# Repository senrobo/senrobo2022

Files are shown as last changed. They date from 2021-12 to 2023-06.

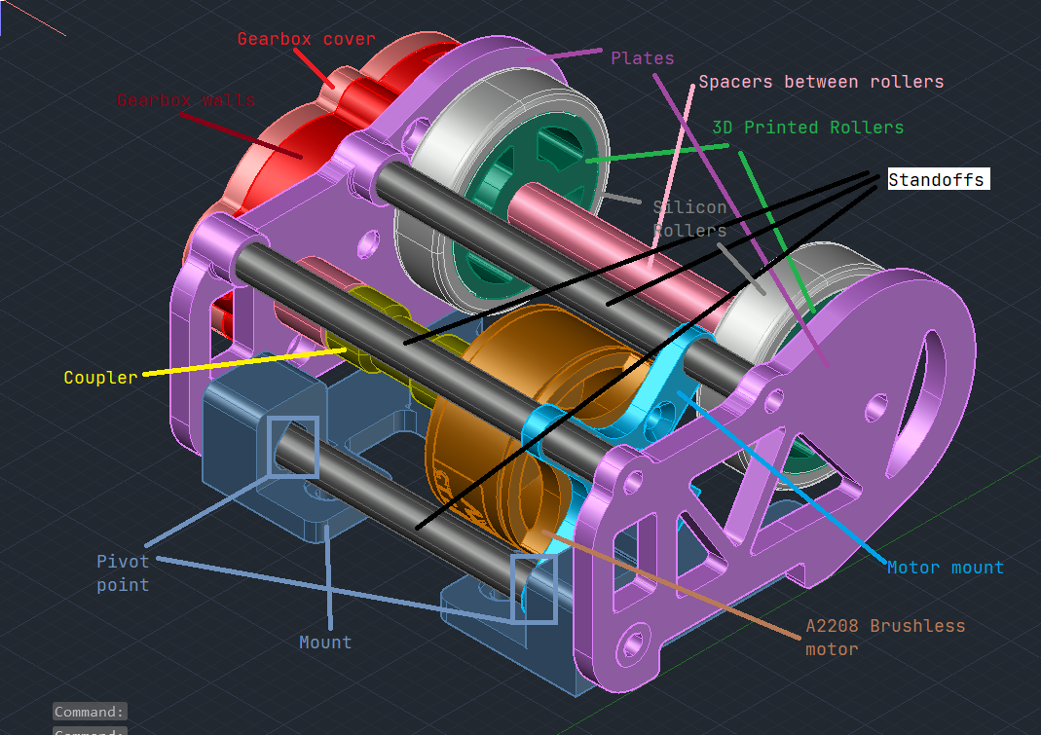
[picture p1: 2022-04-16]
logbook/dribbler5.png

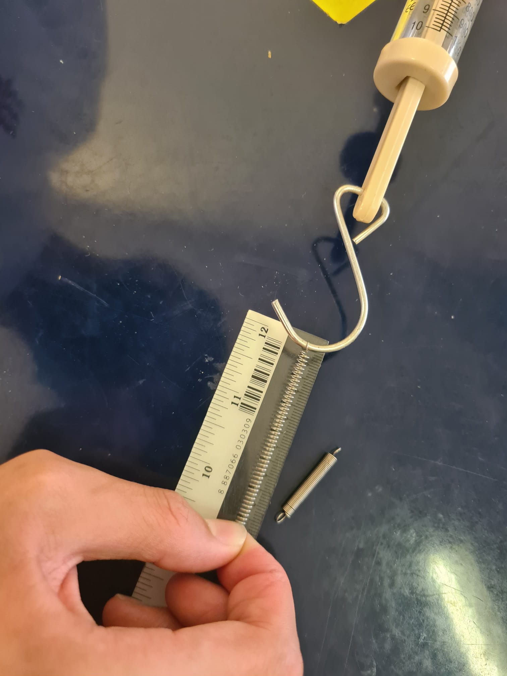
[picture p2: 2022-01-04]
research/spring-test.jpeg

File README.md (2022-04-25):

# Sentinels Robotics

Yay we passed the 100th commit milestone
400 Commit milestone

## Checklist

### Mechanical

- Kicker Done on 20/1/2022

### Parts used

| Part Name | Part Description |
| --- | --- |
| OpenMV H7/R7 | Camera |
| MUX | Multiplexer (https://www.ti.com/lit/ds/symlink/cd74hc4067.pdf) |

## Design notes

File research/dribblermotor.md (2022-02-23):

 10 :40pm: Dribbler motor was too fat and heavy, although it met criteria, it does not meet the weight

had to find for alternatives

went online and read up

basically this website has the impt shit

https://www.rotordronepro.com/understanding-kv-ratings/

so, the higher the KV = more heat = sucks ass = weak ass torque cos the whatever RPM stupid shit is like fucking calculated when the motor is "free moving" so the motor is not underload which is not what we want as our dribbler is always under load

asked the seniors why they were using a super low kv motor 820kV

referred to other lw teams and saw that they were using the A2208 not the A2212 which i was considering to use

shit is fucking autism

why the senior gear down cos the Open ball light as fuck

11:52pm : Now senior said the dribbler is useless cos the matches are all so fast fucking pased what fuck

why am i here just to suffer

<hr></hr>

###### Bern Jia Min Luo Yee Haw *—* 26/11/2021 at 11:56 PM

and vibrations become amplified at such high speeds

###### jh *—*  26/11/2021at 11:56 PM

   anw ir ball need higher rpm

   smaller motor usually rpm bigger so

   maybe ur gearing wont even have to change at all

   win

<hr></hr>

in conclusion, 

###### beanstalk *—* 26/11/2021 at 11:56 PM

lightweight matches are super fast paced lol if they ram into u and your dribbler is shit and loses control of the ball then there really isnt a point in having 1

Vincent - 11/26/2021

what tf its aldy 12

taobao time ezpz

its not ezpz

stupid piece of shit

Vincent11/27/2021

Fuck dribbler not enough space

Vincent 4/1/2022

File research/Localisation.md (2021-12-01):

# Why we dont fucking use ultrasonic

The teensy doesnt output 5V but the ultrasonic sensor need 3.3V volt

Considered usinng logic level converter but quite stupid

So condluded to use camera + compass localisation

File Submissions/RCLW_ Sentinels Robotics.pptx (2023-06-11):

## Sentinels

Hwa Chong Institution

Vincent Cayadi, Zhu Yunsong

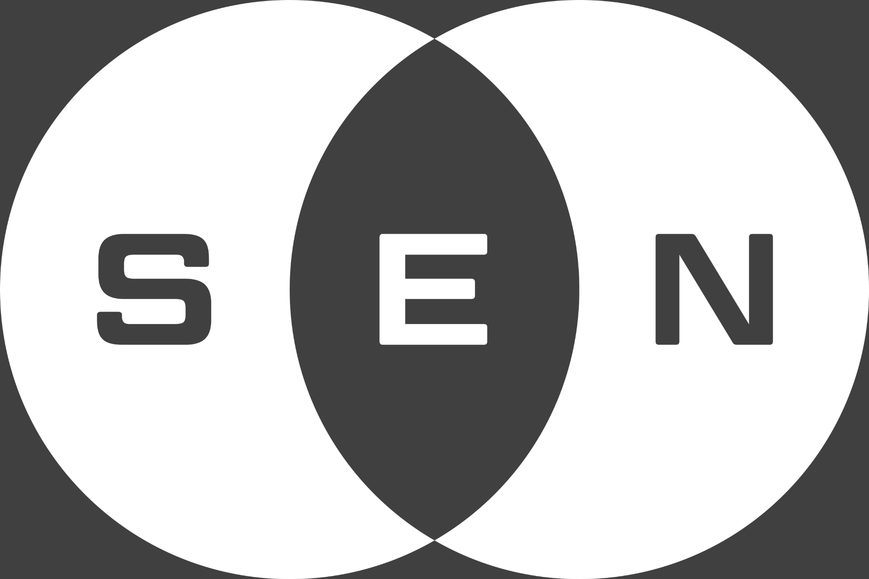
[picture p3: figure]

## Table of contents 1/ Introduction 2/ Mechanical 3/ Electrical 4/ Programming

Background information about our team

Hardware and design aspect of our robot

PCB Design and electronics

Program and algorithms of out robot

## Intro- duction 1/

The 2 man team from Hwa Chong Institution

## Mechanical 2/

Mechanism and elements of our robot

## Layer 1

- Motor
- Slope

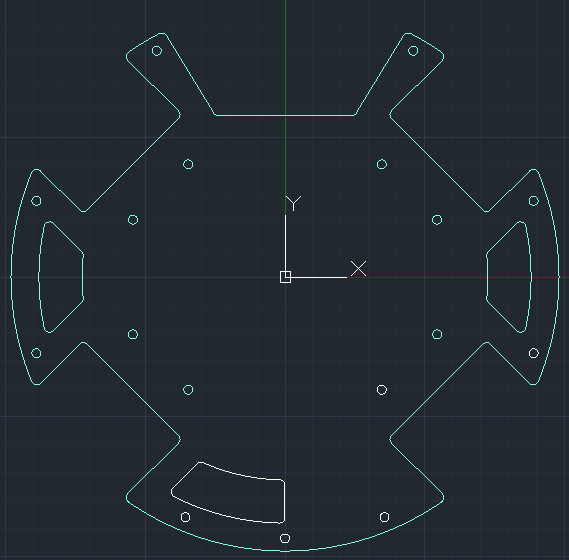
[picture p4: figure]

## Motor Layout Omni-directional 45° Layout

Wheels are 3D printed, with rubber rollers perpendicular to the wheel to make it omnidirectional

Such a layout allows the robot to move in all directions by controlling speed, power and direction of each individual wheel.

## Layer 2

- Dribbler with catchment area in front
- Rec. hole on left for jumper cable
- Rec. hole in center for kicker rack
- Rec. hole on right for servo
- Hole at the back for battery mount

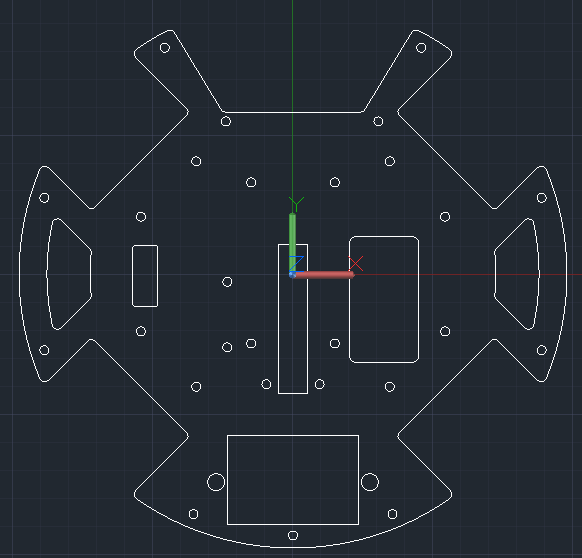
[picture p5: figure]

## Layer 3

Houses our brains
Teensy 4.0 located here
IR Sensor placed here for the highest point of the ball
Camera is also located here
Have a 5 point connection to layer 2 so that the camera won't be shakey

- Copy this slide

## Problems

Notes: Taobao and Senior hogging the printers

## Electrical 3/

Elec go boom

## Schematic

- Layer 1
- Unchanged
- Layer 2
- GND Plane
- Layer 3
- Compass elec shoved there
- Layer 4
- Removed all the elec

## PCB : Layer 1

- LED Ring
- Motor Drivers
- 5V Step Down
- 3V Step Down

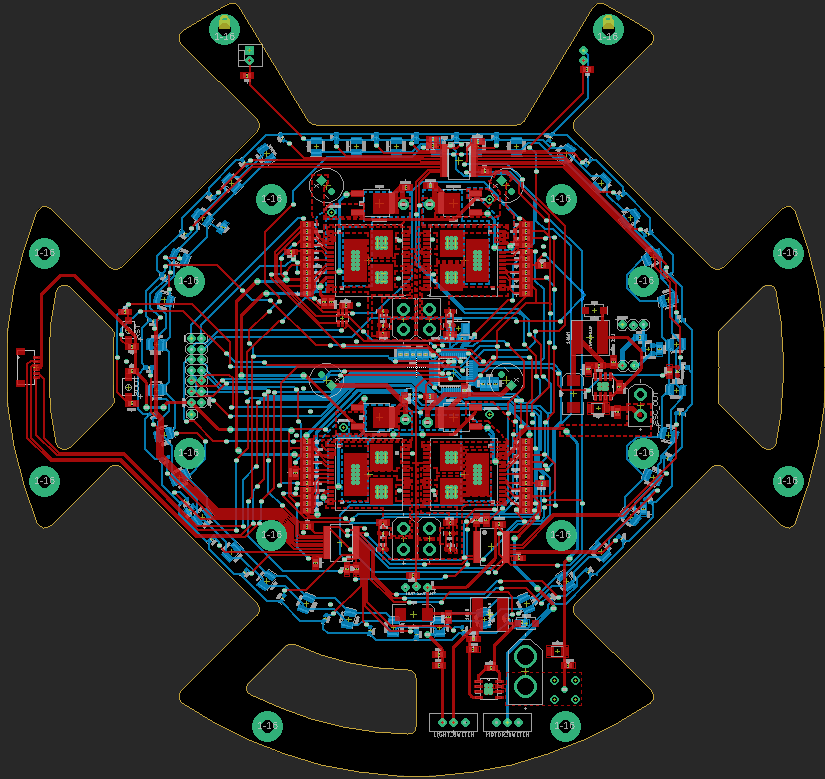
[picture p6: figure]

## PCB : Layer 2

- GND Plane
  - Block Off the Electromagnetic field of the Motor to shield the compass from the field

## PCB : Layer 3

- IR Sensors
- OpenMV Camera
- Compass Components

## Programming: Conceptual 4/

## Camera Localisation

- Removed TOF so how?
- <insert transcendence pic>

## Closing Thoughts

## Thanks!

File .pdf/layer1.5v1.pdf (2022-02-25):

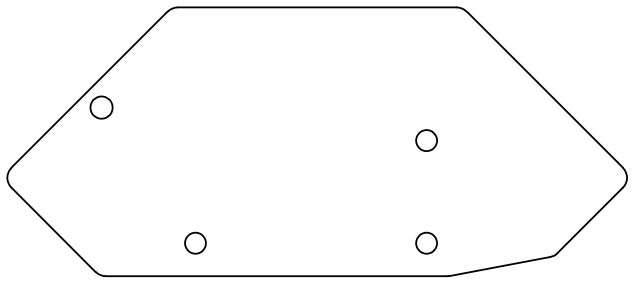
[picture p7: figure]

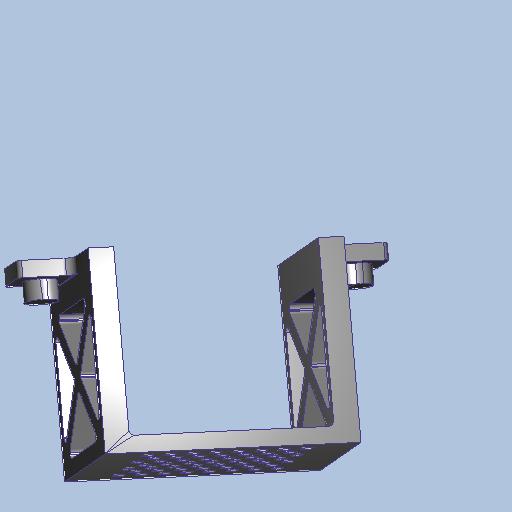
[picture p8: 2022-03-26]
.stl/test/Design 1/Scenario 1/thumbnail.jpg

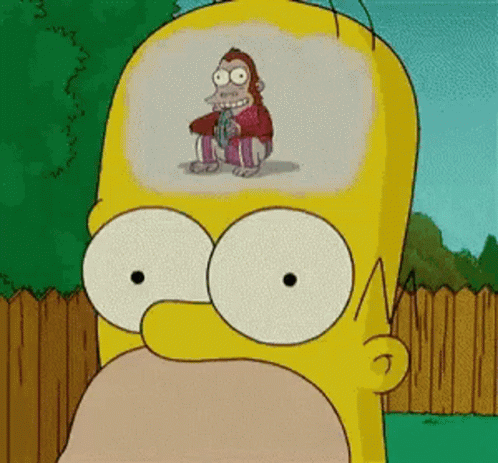
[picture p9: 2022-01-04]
research/homermonkey.gif

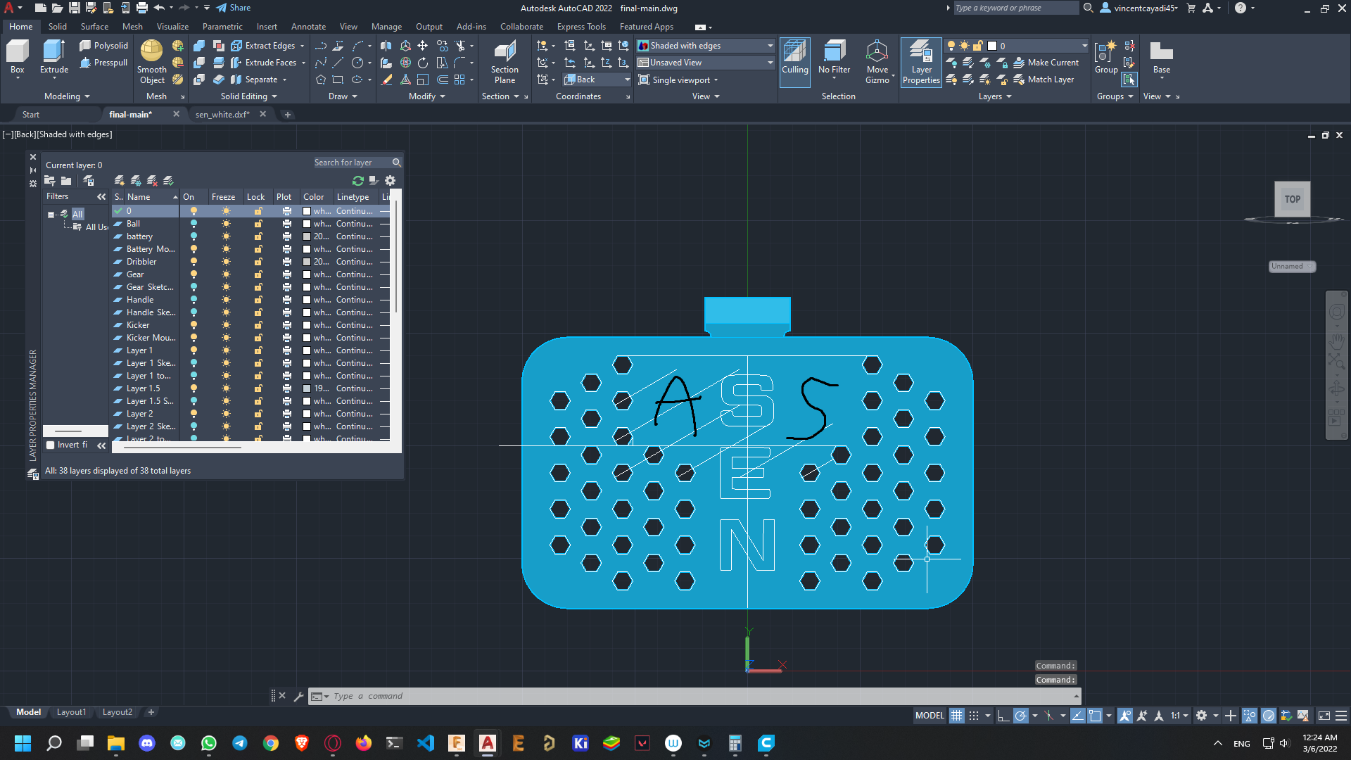
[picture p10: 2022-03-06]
research/senAss.png

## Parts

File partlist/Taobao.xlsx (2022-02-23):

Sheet: Mech
Part Type | Part Name | Decription | Source | Unit Price (¥) | Quantity needed | Quantitiy bought | Total Price (¥) | Total Price (SGD)
Aluminium Stands | M3*37 D=5mm | Stands from Layer 1 to 2 | https://item.taobao.com/item.htm?spm=a1z09.2.0.0.1df82e8d7MtmSg&id=544763051390&_u=230vu5iq6340 | ¥1.50 | 8 | 0 | ¥12.00 | $2.40
Aluminium Stands |  | Stands from Layer 2 to 3 | https://item.taobao.com/item.htm?spm=a1z09.2.0.0.1df82e8d7MtmSg&id=544763051390&_u=230vu5iq6340 | ¥0.00 | 0 | 0 | ¥0.00 | $0.00
Aluminium Stands | M3*20 D=5mm | Front Kicker | https://item.taobao.com/item.htm?spm=a1z09.2.0.0.1df82e8d7MtmSg&id=544763051390&_u=230vu5iq6340 | ¥1.20 | 2 | 0 | ¥2.40 | $0.48
Aluminium Stands | M3*15 D=5mm | Back Kicker | https://item.taobao.com/item.htm?spm=a1z09.2.0.0.1df82e8d7MtmSg&id=544763051390&_u=230vu5iq6340 | ¥1.00 | 2 | 0 | ¥2.00 | $0.40
Metal Nuts |  | a lot |  | ¥0.00 | 0 | 0 | ¥0.00 | $0.00
M3 Screws |  | a lot |  | ¥0.00 | 0 | 0 | ¥0.00 | $0.00
Headless screws |  | a lot |  | ¥0.00 | 0 | 0 | ¥0.00 | $0.00
Extension Springs | 0.4*4*30 | Kicker Mechanism | https://item.taobao.com/item.htm?spm=a1z09.2.0.0.61472e8dM5d2jk&id=522768077711&_u=n30vu5iqd1c4&mt= | ¥3.25 | 1 | 0 | ¥3.25 | $0.65
Servo | MG90S | Servo For kicker |  | ¥0.00 | 0 | 0 | ¥0.00 | $0.00
Heat Sinks | 散热片 8.8*8.8*5MM (黑色) | Heatsink for Motor Driver | https://item.taobao.com/item.htm?id=565186396799&ns=1&abbucket=14 (https://item.taobao.com/item.htm?spm=a230r.1.14.21.5b804308qjOPfB&id=565186396799&ns=1&abbucket=14) | ¥0.24 | 16 | 0 | ¥3.84 | $0.77

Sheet: Elec - Layer 1
Qty | Value | Device | Package | Parts | Description | PROD_ID | SF_ID | SF_SKU | VALUE.1 | Column1
2 | 220uF | 100UF-POLAR-EIA7343-10V-10%(TANT) | EIA7343 | 1C4, 1C7 | 100ÂµF polarized capacitors | CAP-07890 |  |  | 100uF
12 | 18AWG | 18AWG | 18AWG | GND_M2A, GND_M2B, GND_M4A, GND_M4B, V_BATT_M1A, V_BATT_M1B, V_BATT_M2A, V_BATT_M2B, V_BATT_M3A, V_BATT_M3B, V_BATT_M4A, V_BATT_M4B
4 | 680uF | 3.5MM_CAP | 3.5MM_CAP | M1C2, M2C2, M3C2, M4C2
36 | 3528LED | 3528LED | 3528 | LD1, LD2, LD3, LD4, LD5, LD6, LD7, LD8, LD9, LD10, LD11, LD12, LD13, LD14, LD15, LD16, LD17, LD18, LD19, LD20, LD21, LD22, LD23, LD24, LD25, LD26, LD27, LD28, LD29, LD30, LD31, LD32, LD33, LD34, LD35, LD36
3 |  | 74HC4067SSOP-24 | SSOP24 | MUX_L1, MUX_L2, MUX_L3
7 | 0.1uF | CAPACITOR0603 | C0603 | 1C5, 1C9, 2C1, 2C2, 2C3, 3C1, 3C2
4 | 1.0uF | CAPACITOR0603 | C0603 | M1C3, M2C3, M3C3, M4C3
3 | 10nF | CAPACITOR0603 | C0603 | 1C3, 1C8, C4
14 | 1uF | CAPACITOR0603 | C0603 | 2C4, 2C5, 2C6, C1, C2, C3, C5, C8, LC1, LC2, LC3, LC4, LC5, LC6
2 | 22pF | CAPACITOR0603 | C0603 | C6, C7
4 | 33nF | CAPACITOR0603 | C0603 | M1C1, M2C1, M3C1, M4C1
2 | 4.7uF | CAPACITOR0603 | C0603 | 1C1, 1C6
2 | 22uF | CAPACITOR1210 | C1210 | 1C2, 1C10
1 |  | CONN_021X02_NO_SILK | 1X02_NO_SILK | LDR | Multi connection point. Often used as Generic Header-pin footprint for 0.1 inch spaced/style header connections
1 |  | CONN_02LOCK | 1X02_LOCK | J1 | Multi connection point. Often used as Generic Header-pin footprint for 0.1 inch spaced/style header connections
1 |  | CONN_02POLAR | MOLEX-1X2 | LED | Multi connection point. Often used as Generic Header-pin footprint for 0.1 inch spaced/style header connections |  | PRT-09918
1 |  | CONN_03LOCK | 1X03_LOCK | ESC_IN | Multi connection point. Often used as Generic Header-pin footprint for 0.1 inch spaced/style header connections
1 | CONN_07X2 | CONN_07X2 | 2X7 | U$15
1 | 8MHz | CRYSTALSMD-5X3.2-2PAD | CRYSTAL-SMD-5X3.2-2PAD | Y1 | Crystals (Generic)
2 | SS54 | DIODE-SCHOTTKY | SMA-DIODE | 1D1, 1D2
2 | 30Î©/1.8A | FERRITE_BEAD-0603 | 0603 | FB1, FB2 | Ferrite Bead (blocks, cores, rings, chokes, etc.) | NDUC-13805 |  |  | 30Î©/1.8A
2 | 10uH | INDUCTORSWPA8040 | SWPA8040 | 1L1, 1L2
1 | STM_LED | LED0603 | LED-0603 | D1 | LED (Generic)
4 | BLUE | LED-BLUE0603 | LED-0603 | M1D2, M2D2, M3D2, M4D2 | Blue SMD LED | DIO-08575 |  |  | BLUE
4 | RED | LED-RED0603 | LED-0603 | M1D1, M2D1, M3D1, M4D1 | Red SMD LED | DIO-00819 |  |  | RED
36 |  | LIGHT_SENSORALS | ALS-PT19 | Q1, Q2, Q3, Q4, Q5, Q6, Q7, Q8, Q9, Q10, Q11, Q12, Q13, Q14, Q15, Q16, Q17, Q18, Q19, Q20, Q21, Q22, Q23, Q24, Q25, Q26, Q27, Q28, Q29, Q30, Q31, Q32, Q33, Q34, Q35, Q36 | Ambient Light Sensors - Phototransistors | IC-11836 | SEN-12566
2 | MOMENTARY_SWITCH_4X3 | MOMENTARY_SWITCH_4X3 | MOMENTARY_SWITCH_4X3 | BOOT, RST
1 | AO3402 | MOSFET-NCH-AO3404A | SOT23-3 | Q37 | N-channel MOSFETs | TRANS-12988 |  |  | 5.8A/30V/35mÎ©
4 | AOD482 | MOSFET-NCH-FDD8780 | DPAK | M1Q1, M2Q1, M3Q1, M4Q1 | N-channel MOSFETs | TRANS-09984 |  |  | 35A/25V/8.5mÎ©
16 | 10k | RESISTOR0603 | R0603 | 1R1, 1R3, M1R8, M1R9, M1R11, M2R8, M2R9, M2R11, M3R8, M3R9, M3R11, M4R8, M4R9, M4R11, R1, R4
29 | 1k | RESISTOR0603 | R0603 | 2R1, 2R2, 2R3, M1R1, M1R2, M1R5, M1R6, M1R7, M1R10, M2R1, M2R2, M2R5, M2R6, M2R7, M2R10, M3R1, M3R2, M3R5, M3R6, M3R7, M3R10, M4R1, M4R2, M4R5, M4R6, M4R7, M4R10, R2, R3
1 | 2M | RESISTOR0603 | R0603 | R6
1 | 2k | RESISTOR0603 | R0603 | LG_R2
1 | 3.24k | RESISTOR0603 | R0603 | 1R4
8 | 3.3k | RESISTOR0603 | R0603 | M1R3, M1R4, M2R3, M2R4, M3R3, M3R4, M4R3, M4R4
3 | 3k | RESISTOR0603 | R0603 | 2R4, 2R5, 2R6
6 | 4.7k | RESISTOR0603 | R0603 | M1R12, M2R12, M3R12, M4R12, R8, R9
1 | 47 | RESISTOR0603 | R0603 | LR1
1 | 470 | RESISTOR0603 | R0603 | R5
1 | 5.9k | RESISTOR0603 | R0603 | 1R2
1 | 500k | RESISTOR0603 | R0603 | R7
1 | SM06B-SRSS-TB | SM06B-SRSS-TB | SM06B-SRSS-TB | X2 | JST SH series header 1.00mm pitch disconnectable crimp style connectors, horizontal (side entry type), 6 pins
2 |  | SN74LVC2G04DBVR | SOT23-6 | MU1, MU2
1 | STM32F103CBT6 | STM32F103CBT6 | LQFP48 | U$2
2 |  | SWITCH-SPDT-PTH-11.6X4.0MM-LOCK | SWITCH_SPDT_PTH_11.6X4.0MM_LOCK | LIGHT_SWITCH, MOTOR_SWITCH | Single Pole, Double Throw (SPDT) Switch | SWCH-08261 |  | COM-00102
2 |  | TPS54X0 | POWERPAD-SOIC-8 | U1, U2
4 | VNH5019 | VNH5019 | POWERSO-30 | M_BL, M_BR, M_FL, M_FR
5 | XT30PB-F | XT30PB-F | XT30PB-F | ESC_OUT, M1J1, M2J1, M3J1, M4J1
1 | XT60XT60PB-M | XT60XT60PB-M | XT60PB-M | U$1

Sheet: Elec - Layer 3
Qty | Value | Device | Package | Parts | Description | PROD_ID | SF_SKU | VALUE.1 | Column1
24 |  | CAPACITOR0603 | C0603 | 3C1, 3C2, 3C3, 3C4, 3C5, 3C6, 3C7, 3C8, 3C9, 3C10, 3C11, 3C12, 3C13, 3C14, 3C15, 3C16, 3C17, 3C18, 3C19, 3C20, 3C21, 3C22, 3C23, 3C24
4 | 1uF | CAPACITOR0603 | C0603 | C1, C2, C3, C5
2 | 22pF | CAPACITOR0603 | C0603 | C6, C7
1 |  | CONN_02LOCK | 1X02_LOCK | J1 | Multi connection point. Often used as Generic Header-pin footprint for 0.1 inch spaced/style header connections
1 |  | CONN_03LOCK | 1X03_LOCK | SERVO_IO | Multi connection point. Often used as Generic Header-pin footprint for 0.1 inch spaced/style header connections
1 | CONN_07X2 | CONN_07X2 | 2X7 | U$14
1 | 8MHz | CRYSTALSMD-5X3.2-2PAD | CRYSTAL-SMD-5X3.2-2PAD | Y1 | Crystals (Generic)
1 | DIP-04SMD | DIP-04SMD | DIPSWITCH-04-SMD | S1 | 4-Position DIP Switch
1 | HC-05 | HC-05 | HC-05 | BLUETOOTH
1 | BLUE | LED0603 | LED-0603 | D1 | LED (Generic)
2 | MOMENTARY_SWITCH_4X3 | MOMENTARY_SWITCH_4X3 | MOMENTARY_SWITCH_4X3 | BOOT, RST
1 | AO3402 | MOSFET-NCH-AO3404A | SOT23-3 | Q2 | N-channel MOSFETs | TRANS-12988 |  | 5.8A/30V/35mÎ©
1 | OPENMV3 | OPENMV3 | OPENMV3 | U$8
6 | 10k | RESISTOR0603 | R0603 | R1, R4, R6, R7, R8, R9
2 | 1k | RESISTOR0603 | R0603 | R2, R3
2 | 4.7k | RESISTOR0603 | R0603 | R12, R13
1 | 470 | RESISTOR0603 | R0603 | R5
1 | SM04B-SRSS-TB | SM04B-SRSS-TB | SM04B-SRSS-TB | 4TH_LAYER | JST SH series header 1.00mm pitch disconnectable crimp style connectors, horizontal (side entry type), 4 pins
1 | SM06B-SRSS-TB | SM06B-SRSS-TB | SM06B-SRSS-TB | X1 | JST SH series header 1.00mm pitch disconnectable crimp style connectors, horizontal (side entry type), 6 pins
1 | STM32F103CBT6 | STM32F103CBT6 | LQFP48 | STM32_IR
2 |  | SWITCH-SPDT-PTH-11.6X4.0MM-LOCK | SWITCH_SPDT_PTH_11.6X4.0MM_LOCK | 3V3_PWR, 5V_PWR | Single Pole, Double Throw (SPDT) Switch | SWCH-08261 | COM-00102
1 | TEENSY_3.5/3.6_NO_MIDDLE | TEENSY_3.5/3.6_NO_MIDDLE | TEENSY_3.5/3.6_NO_MIDDLE | U$1
24 | TSSP58038 | TSSP58038 | TSSP58038 | 3U1, 3U2, 3U3, 3U4, 3U5, 3U6, 3U7, 3U8, 3U9, 3U10, 3U11, 3U12, 3U13, 3U14, 3U15, 3U16, 3U17, 3U18, 3U19, 3U20, 3U21, 3U22, 3U23, 3U24

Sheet: Elec - Layer 4
Qty | Value | Device | Package | Parts | Description | PROD_ID | SF_SKU | Column1
16 |  | LED0603 | LED-0603 | 1D1, 1D2, 1D3, 1D4, 1D5, 1D6, 1D7, 1D8, 1D9, 1D10, 1D11, 1D12, 1D13, 1D14, 1D15, 1D16 | LED (White)
1 |  | SWITCH-SPDT-PTH-11.6X4.0MM-LOCK | SWITCH_SPDT_PTH_11.6X4.0MM_LOCK | 3V3_PWR | Single Pole, Double Throw (SPDT) Switch | SWCH-08261 | COM-00102
2 | 10k | RESISTOR0603 | R0603 | R1, R4
3 | 1k | RESISTOR0603 | R0603 | R2, R3, R5
4 | 1uF | CAPACITOR0603 | C0603 | C1, C2, C3, C5
2 | 22pF | CAPACITOR0603 | C0603 | C6, C7
8 | 470 | RESISTOR0603 | R0603 | 1R1, 1R2, 1R3, 1R4, 1R5, 1R6, 1R7, 1R8
1 | 8MHz | CRYSTALSMD-5X3.2-2PAD | CRYSTAL-SMD-5X3.2-2PAD | Y1 | Crystals (Generic)
1 | BLUE | LED0603 | LED-0603 | D1 | LED (Generic)
1 | BNO055 | BNO055 | BNO055 | COMPASS
3 | MOMENTARY_SWITCH_4X3 | MOMENTARY_SWITCH_4X3 | MOMENTARY_SWITCH_4X3 | BOOT, COMPASS_RST, RST
1 | SM04B-SRSS-TB | SM04B-SRSS-TB | SM04B-SRSS-TB | 3RD_LAYER | JST SH series header 1.00mm pitch disconnectable crimp style connectors, horizontal (side entry type), 4 pins
1 | SM06B-SRSS-TB | SM06B-SRSS-TB | SM06B-SRSS-TB | PROGRAMMER | JST SH series header 1.00mm pitch disconnectable crimp style connectors, horizontal (side entry type), 6 pins
1 | STM32F103CBT6 | STM32F103CBT6 | LQFP48 | STM32

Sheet: Master
Qty | Value | Device | Package | Description | Qty for 2 bots | Final Qty
Others
2 | 30Î©/1.8A | FERRITE_BEAD-0603 | 603 | Ferrite Bead (blocks, cores, rings, chokes, etc.) | 4 | 10
36 |  | LIGHT_SENSORALS | ALS-PT19 | Ambient Light Sensors - Phototransistors | 72 | 90
3 | 8MHz | CRYSTALSMD-5X3.2-2PAD | CRYSTAL-SMD-5X3.2-2PAD | Crystals (Generic) | 6 | 12
1 | DIP-04SMD | DIP-04SMD | DIPSWITCH-04-SMD | 4-Position DIP Switch | 2 | 8
2 | SS54 | DIODE-SCHOTTKY | SMA-DIODE |  | 4 | 10
2 |  | SN74LVC2G04DBVR | SOT23-6 |  | 4 | 10
3 |  | 74HC4067SSOP-24 | SSOP24 | Multiplexer | 6 | 9
2 | 10uH | INDUCTORSWPA8040 | SWPA8040 |  | 4 | 10
2 |  | TPS54X0 | POWERPAD-SOIC-8 |  | 4 | 10
Resistors and Capacitors
24 | 10k | RESISTOR0603 | R0603 |  | 48 | 100
34 | 1k | RESISTOR0603 | R0603 |  | 68 | 140
1 | 2k | RESISTOR0603 | R0603 |  | 2 | 8
1 | 2M | RESISTOR0603 | R0603 |  | 2 | 8
1 | 3.24k | RESISTOR0603 | R0603 |  | 2 | 8
8 | 3.3k | RESISTOR0603 | R0603 |  | 16 | 35
3 | 3k | RESISTOR0603 | R0603 |  | 6 | 15
8 | 4.7k | RESISTOR0603 | R0603 |  | 16 | 35
1 | 47 | RESISTOR0603 | R0603 |  | 2 | 8
10 | 470 | RESISTOR0603 | R0603 |  | 20 | 40
1 | 500k | RESISTOR0603 | R0603 |  | 2 | 8
1 | 5.9k | RESISTOR0603 | R0603 |  | 2 | 8
7 | 0.1uF | CAPACITOR0603 | C0603 |  | 14 | 30
4 | 1.0uF | CAPACITOR0603 | C0603 |  | 8 | 16
3 | 10nF | CAPACITOR0603 | C0603 |  | 6 | 12
46 | 1uF | CAPACITOR0603 | C0603 |  | 92 | 150
8 | 22pF | CAPACITOR0603 | C0603 |  | 16 | 30
4 | 33nF | CAPACITOR0603 | C0603 |  | 8 | 20
2 | 4.7uF | CAPACITOR0603 | C0603 |  | 4 | 10
4 | 680uF | 3.5MM_CAP | 3.5MM_CAP |  | 8 | 20
2 | 220uF | 100UF-POLAR-EIA7343-10V-10%(TANT) | EIA7343 | 100ÂµF polarized capacitors | 4 | 10
Connectors
5 | XT30PB-F | XT30PB-F | XT30PB-F | XT30 | 10 | 15
1 | XT60XT60PB-M | XT60XT60PB-M | XT60PB-M | XT60 | 2 | 5
5 | SM04B-SRSS-TB | SM04B-SRSS-TB | SM04B-SRSS-TB | JST SH series header 1.00mm pitch disconnectable crimp style connectors, horizontal (side entry type), 4 pins | 10 | 15
LEDS
16 | WHITE | LED-WHITE0603 | LED-0603 | LED (White) | 32 | 40
7 | BLUE | LED-BLUE0603 | LED-0603 | Blue SMD LED | 14 | 18
4 | RED | LED-RED0603 | LED-0603 | Red SMD LED | 8 | 10
36 | 3528LED | 3528LED | 3528 | For Layer 1 Light Sensor | 72 | 100
Connectors
5 | Switch | SWITCH-SPDT-PTH-11.6X4.0MM-LOCK | SWITCH_SPDT_PTH_11.6X4.0MM_LOCK | 3 Pin Switch | 10 | 15
7 | Switch | MOMENTARY_SWITCH_4X3 | MOMENTARY_SWITCH_4X3 | Button | 14 | 20
Main Components
1 | HC-05 | HC-05 | HC-05 | Bluetooth | 2 | 2
3 | STM32F103CBT6 | STM32F103CBT6 | LQFP48 | STM32 | 6 | 8
1 | OPENMV3 | OPENMV3 | OPENMV3 | Camera | 2 | 2
1 | BNO055 | BNO055 | BNO055 | Compass | 2 | 2
24 | TSSP58038 | TSSP58038 | TSSP58038 | IR Sensors | 48 | 81
MOSFET
2 | AO3402 | MOSFET-NCH-AO3404A | SOT23-3 | N-channel MOSFETs | 4 | 10
4 | AOD482 | MOSFET-NCH-FDD8780 | DPAK | N-channel MOSFETs | 8 | 16

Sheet: Sheet1
Qty | Value | Device | Package | Description | Qty for 2 bots | Final Qty
Others
2 | 30Î©/1.8A | FERRITE_BEAD-0603 | 603 | Ferrite Bead (blocks, cores, rings, chokes, etc.) | 4 | 10
Resistors and Capacitors
1 | 2k | RESISTOR0603 | R0603 |  | 2 | 8
1 | 2M | RESISTOR0603 | R0603 |  | 2 | 8
10 | 470 | RESISTOR0603 | R0603 |  | 20 | 40
2 | 220uF | 100UF-POLAR-EIA7343-10V-10%(TANT) | EIA7343 | 100ÂµF polarized capacitors | 4 | 10

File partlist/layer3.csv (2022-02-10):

Qty | Value | Device | Package | Parts | Description | PROD_ID | SF_SKU | VALUE
24 |  | CAPACITOR0603 | C0603 | 3C1, 3C2, 3C3, 3C4, 3C5, 3C6, 3C7, 3C8, 3C9, 3C10, 3C11, 3C12, 3C13, 3C14, 3C15, 3C16, 3C17, 3C18, 3C19, 3C20, 3C21, 3C22, 3C23, 3C24
1 |  | CONN_02LOCK | 1X02_LOCK | J1 | Multi connection point. Often used as Generic Header-pin footprint for 0.1 inch spaced/style header connections
1 |  | CONN_03LOCK | 1X03_LOCK | SERVO_IO | Multi connection point. Often used as Generic Header-pin footprint for 0.1 inch spaced/style header connections
2 |  | SWITCH-SPDT-PTH-11.6X4.0MM-LOCK | SWITCH_SPDT_PTH_11.6X4.0MM_LOCK | 3V3_PWR, 5V_PWR | Single Pole, Double Throw (SPDT) Switch | SWCH-08261 | COM-00102
6 | 10k | RESISTOR0603 | R0603 | R1, R4, R6, R7, R8, R9
2 | 1k | RESISTOR0603 | R0603 | R2, R3
4 | 1uF | CAPACITOR0603 | C0603 | C1, C2, C3, C5
2 | 22pF | CAPACITOR0603 | C0603 | C6, C7
2 | 4.7k | RESISTOR0603 | R0603 | R12, R13
1 | 470 | RESISTOR0603 | R0603 | R5
1 | 8MHz | CRYSTALSMD-5X3.2-2PAD | CRYSTAL-SMD-5X3.2-2PAD | Y1 | Crystals (Generic)
1 | AO3402 | MOSFET-NCH-AO3404A | SOT23-3 | Q2 | N-channel MOSFETs | TRANS-12988 |  | 5.8A/30V/35mΩ
1 | BLUE | LED0603 | LED-0603 | D1 | LED (Generic)
1 | CONN_07X2 | CONN_07X2 | 2X7 | U$14
1 | DIP-04SMD | DIP-04SMD | DIPSWITCH-04-SMD | S1 | 4-Position DIP Switch
1 | HC-05 | HC-05 | HC-05 | BLUETOOTH
2 | MOMENTARY_SWITCH_4X3 | MOMENTARY_SWITCH_4X3 | MOMENTARY_SWITCH_4X3 | BOOT, RST
1 | OPENMV3 | OPENMV3 | OPENMV3 | U$8
1 | SM04B-SRSS-TB | SM04B-SRSS-TB | SM04B-SRSS-TB | 4TH_LAYER | JST SH series header 1.00mm pitch disconnectable crimp style connectors, horizontal (side entry type), 4 pins
1 | SM06B-SRSS-TB | SM06B-SRSS-TB | SM06B-SRSS-TB | X1 | JST SH series header 1.00mm pitch disconnectable crimp style connectors, horizontal (side entry type), 6 pins
1 | STM32F103CBT6 | STM32F103CBT6 | LQFP48 | STM32_IR
1 | TEENSY_3.5/3.6_NO_MIDDLE | TEENSY_3.5/3.6_NO_MIDDLE | TEENSY_3.5/3.6_NO_MIDDLE | U$1
24 | TSSP58038 | TSSP58038 | TSSP58038 | 3U1, 3U2, 3U3, 3U4, 3U5, 3U6, 3U7, 3U8, 3U9, 3U10, 3U11, 3U12, 3U13, 3U14, 3U15, 3U16, 3U17, 3U18, 3U19, 3U20, 3U21, 3U22, 3U23, 3U24

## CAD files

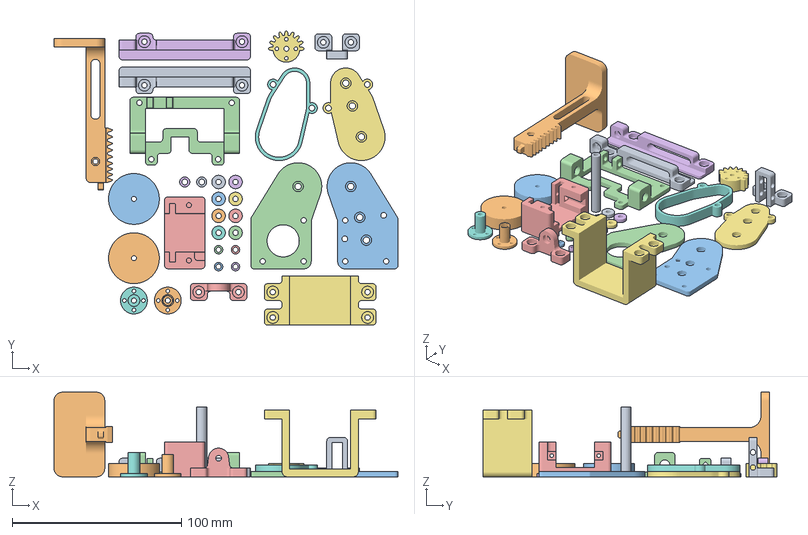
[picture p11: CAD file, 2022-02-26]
.3mf/allparts_cura.3mf
203.1 x 173.7 x 50.0 mm
Motor Spacer v1.3mf
Motor Spacer v1.3mf(1)
Motor Spacer v1.3mf(2)
Motor Spacer v1.3mf(3)
Motor Spacer v1.3mf(4)
Motor Spacer v1.3mf(5)
Motor Spacer v1.3mf(6)
Motor Spacer v1.3mf(7)
dribblerspacerlarge.3mf
dribblerrollerleft.3mf
dribblerrollerright.3mf
dribblerplateright.3mf
servomount.3mf
kickermountleft.3mf
dribblergearboxcover.3mf
dribblergearboxwalls.3mf
kickermountright.3mf
kickerbody.3mf
dribblerplaetleft.3mf
dribblermount.3mf
servoaxleholder.3mf
dribblerspacersmall.3mf
gear.3mf
servohornleft.3mf
limitswitchmount.3mf
servohornright.3mf
2mmstands.3mf(1)
2mmstands.3mf(4)
2mmstands.3mf(5)
2mmstands.3mf(7)
batterymount.stl

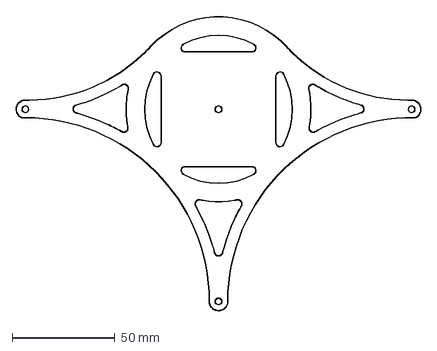
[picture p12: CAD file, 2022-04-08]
.dxf/layer4v5.dxf
197.0 x 143.2 mm

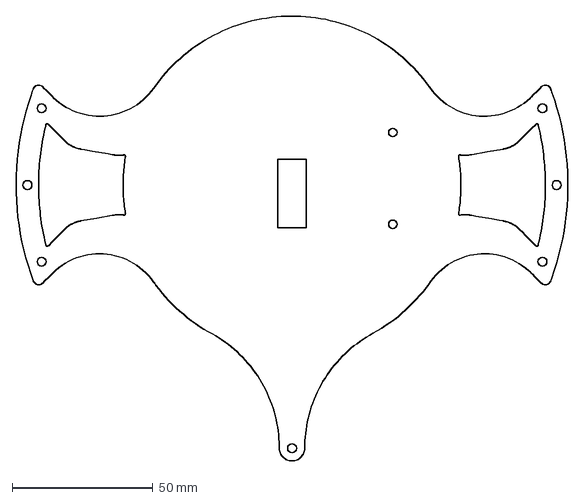
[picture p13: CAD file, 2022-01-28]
.dxf/test/layer3test.dxf
196.0 x 158.0 mm

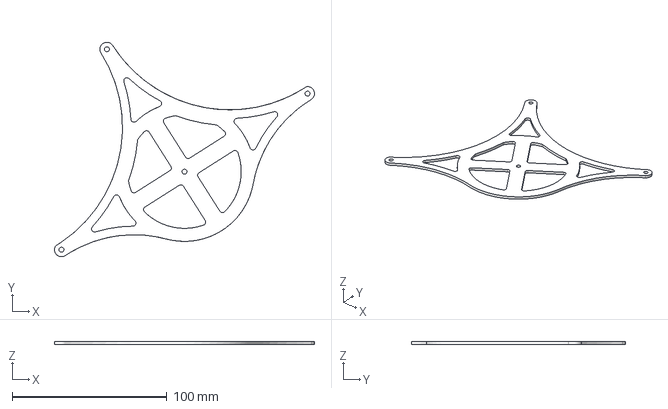
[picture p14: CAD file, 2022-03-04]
.iges/layer4.igs
167.7 x 138.3 x 2.00 mm

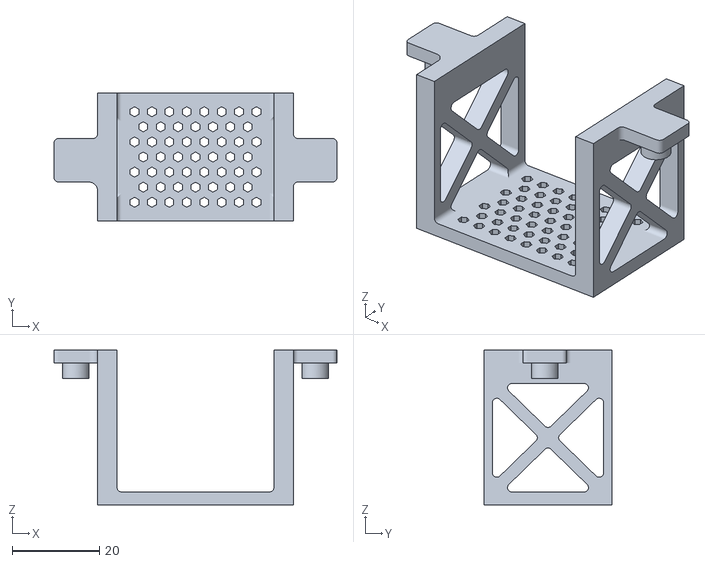
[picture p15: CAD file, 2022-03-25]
.stl/battery mount/batterymountv3.stl
65.0 x 29.5 x 35.6

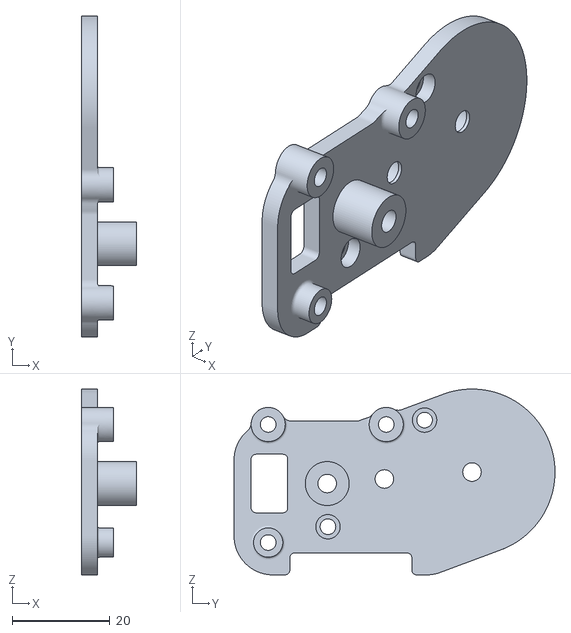
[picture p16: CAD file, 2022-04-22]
.stl/dribbler/dribblerrplatev2.stl
11.2 x 65.7 x 38.1

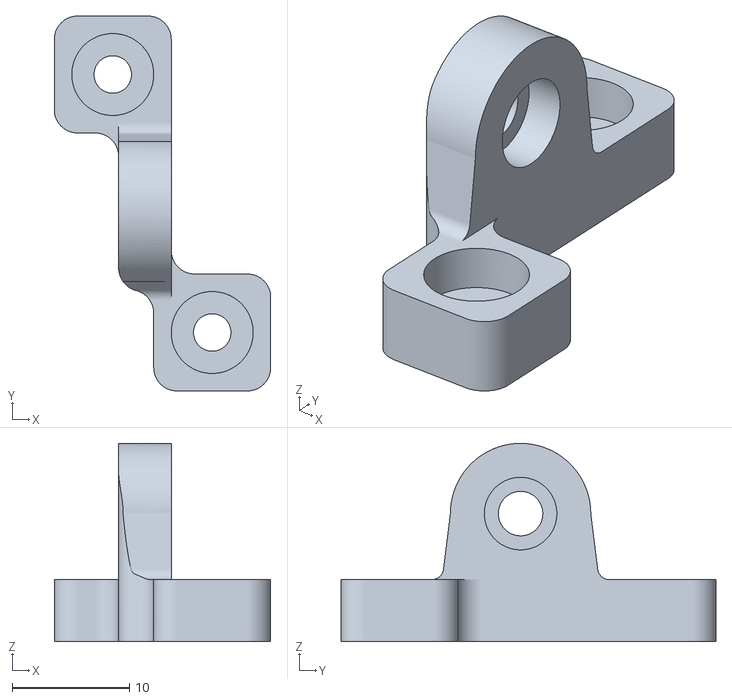
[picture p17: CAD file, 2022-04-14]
.stl/kicker system/bearingmountv1.stl
18.5 x 32.0 x 16.9

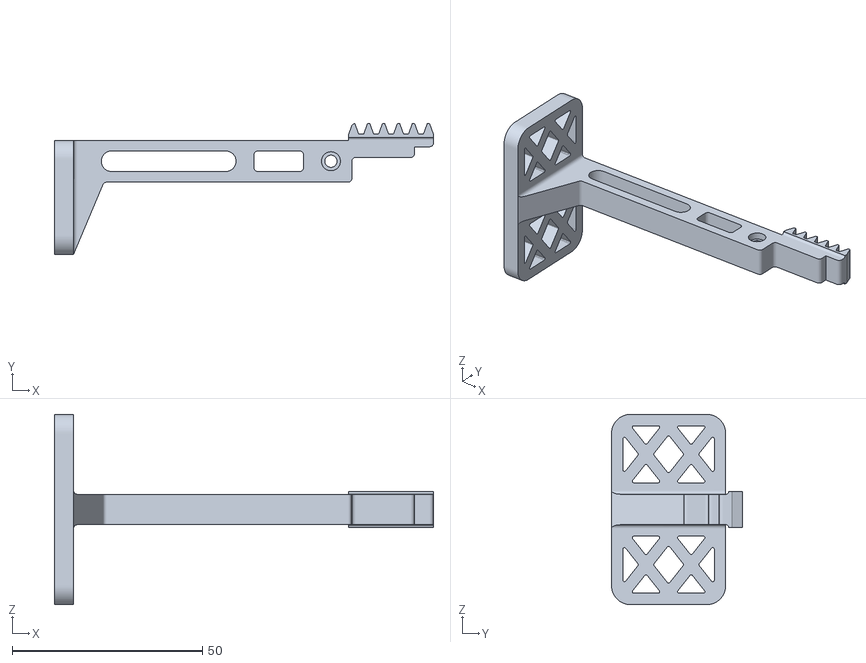
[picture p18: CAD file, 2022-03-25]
.stl/kicker system/test/kickerv8.stl
99.6 x 34.4 x 50.0

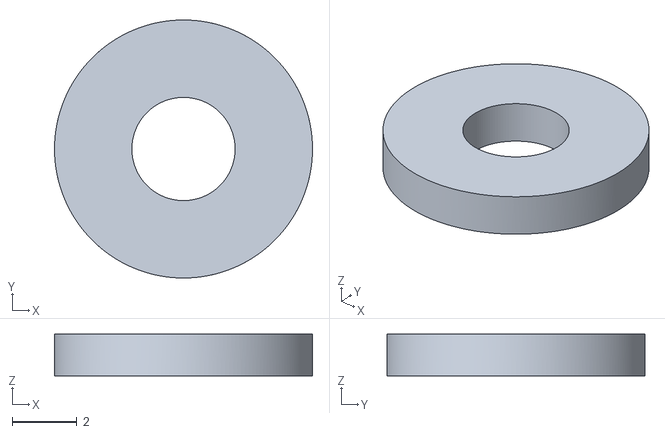
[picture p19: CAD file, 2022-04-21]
.stl/layer41mmspacers.stl
8.00 x 8.00 x 1.30

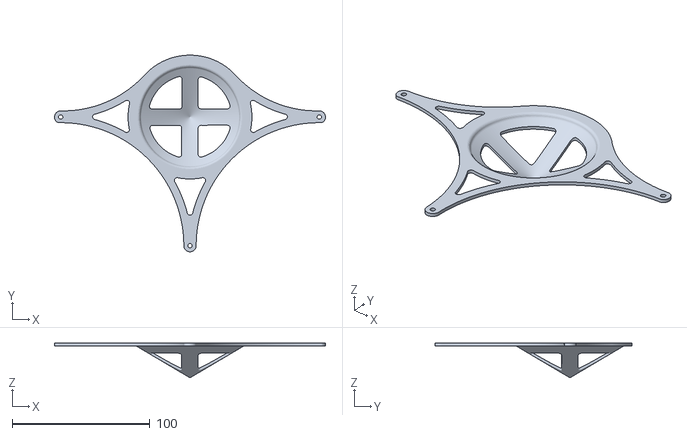
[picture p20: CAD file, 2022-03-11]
.stl/mirror/mirrorLayer4v5.stl
197.0 x 143.0 x 25.2

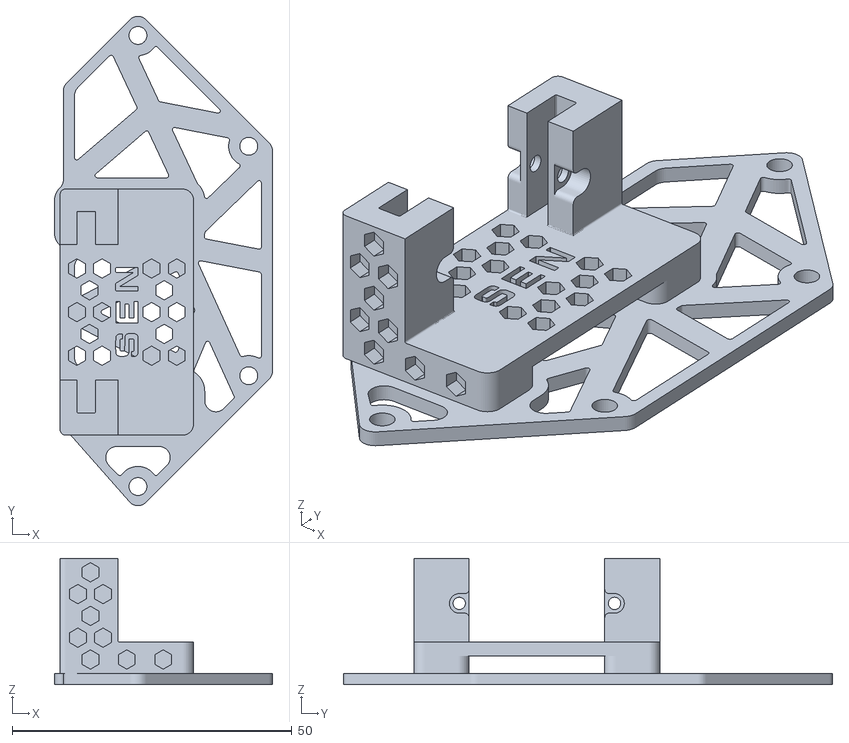
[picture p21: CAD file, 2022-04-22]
.stl/servo mount/layer1.5servomountv7.stl
39.0 x 87.4 x 22.6

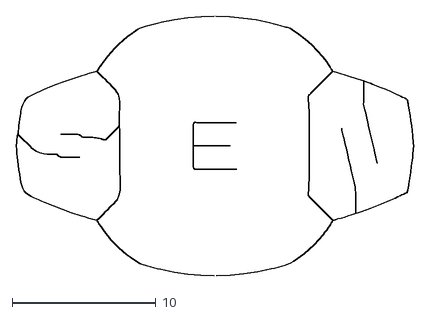
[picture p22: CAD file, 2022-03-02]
graphics/sen/.dxf/sen_white spline.dxf
27.6 x 18.0

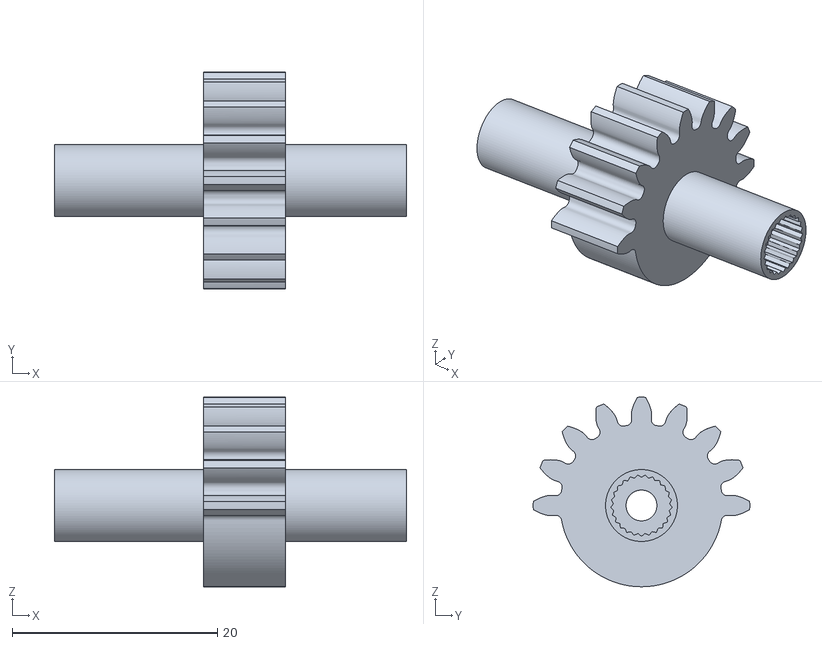
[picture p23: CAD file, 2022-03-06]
senttosrc/v2/strong/gear - Rotate this model 90 degrees.stl
34.3 x 21.1 x 18.5

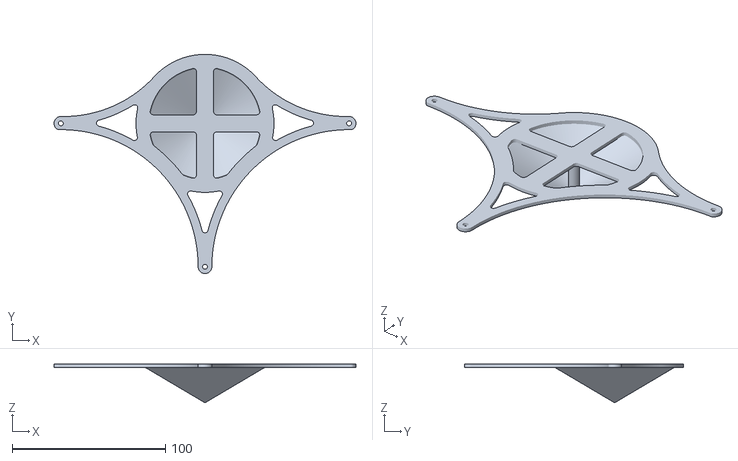
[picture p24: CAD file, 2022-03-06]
senttosrc/v2/weak/Rotate All these models 180 degrees/mirrorLayer4.stl
197.0 x 143.0 x 25.2

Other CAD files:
.dwg/assets/olddribbler.dwg
.dwg/prototype/kicker/kicker-head-1.dwg
.stl/test/Design 1/batteryMount.stl
graphics/sen/.dwg/sen_vert.dwg
.3mf/2mmstands.3mf
.3mf/batterymount.stl
.3mf/dribblergearboxcover.3mf
.3mf/dribblergearboxwalls.3mf
.3mf/dribblermount.3mf
.3mf/dribblerplaetleft.3mf
.3mf/dribblerplateright.3mf
.3mf/dribblerrollerleft.3mf
.3mf/dribblerrollerright.3mf
.3mf/dribblerspacerlarge.3mf
.3mf/dribblerspacersmall.3mf
.3mf/gear.3mf
.3mf/kickerbody.3mf
.3mf/kickermountleft.3mf
.3mf/kickermountright.3mf
.3mf/limitswitchmount.3mf
.3mf/motorspacer.3mf
.3mf/servoaxleholder.3mf
.3mf/servohornleft.3mf
.3mf/servohornright.3mf
.3mf/servomount.3mf
.dwg/assets/a2208motor.dwg
.dwg/assets/a2212motor.dwg
.dwg/assets/bearinginset.dwg
.dwg/assets/blackflipswitch.dwg
.dwg/assets/dribbler.dwg
.dwg/assets/gearandgearrack.dwg
.dwg/assets/kicker.dwg
.dwg/assets/layer2.dwg
.dwg/assets/layer3.dwg
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

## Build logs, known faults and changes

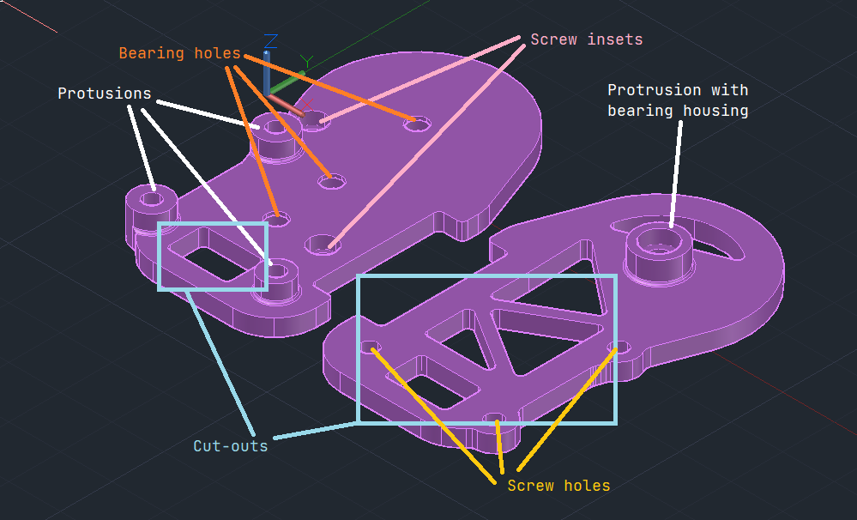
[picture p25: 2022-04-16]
logbook/dribbler6.png

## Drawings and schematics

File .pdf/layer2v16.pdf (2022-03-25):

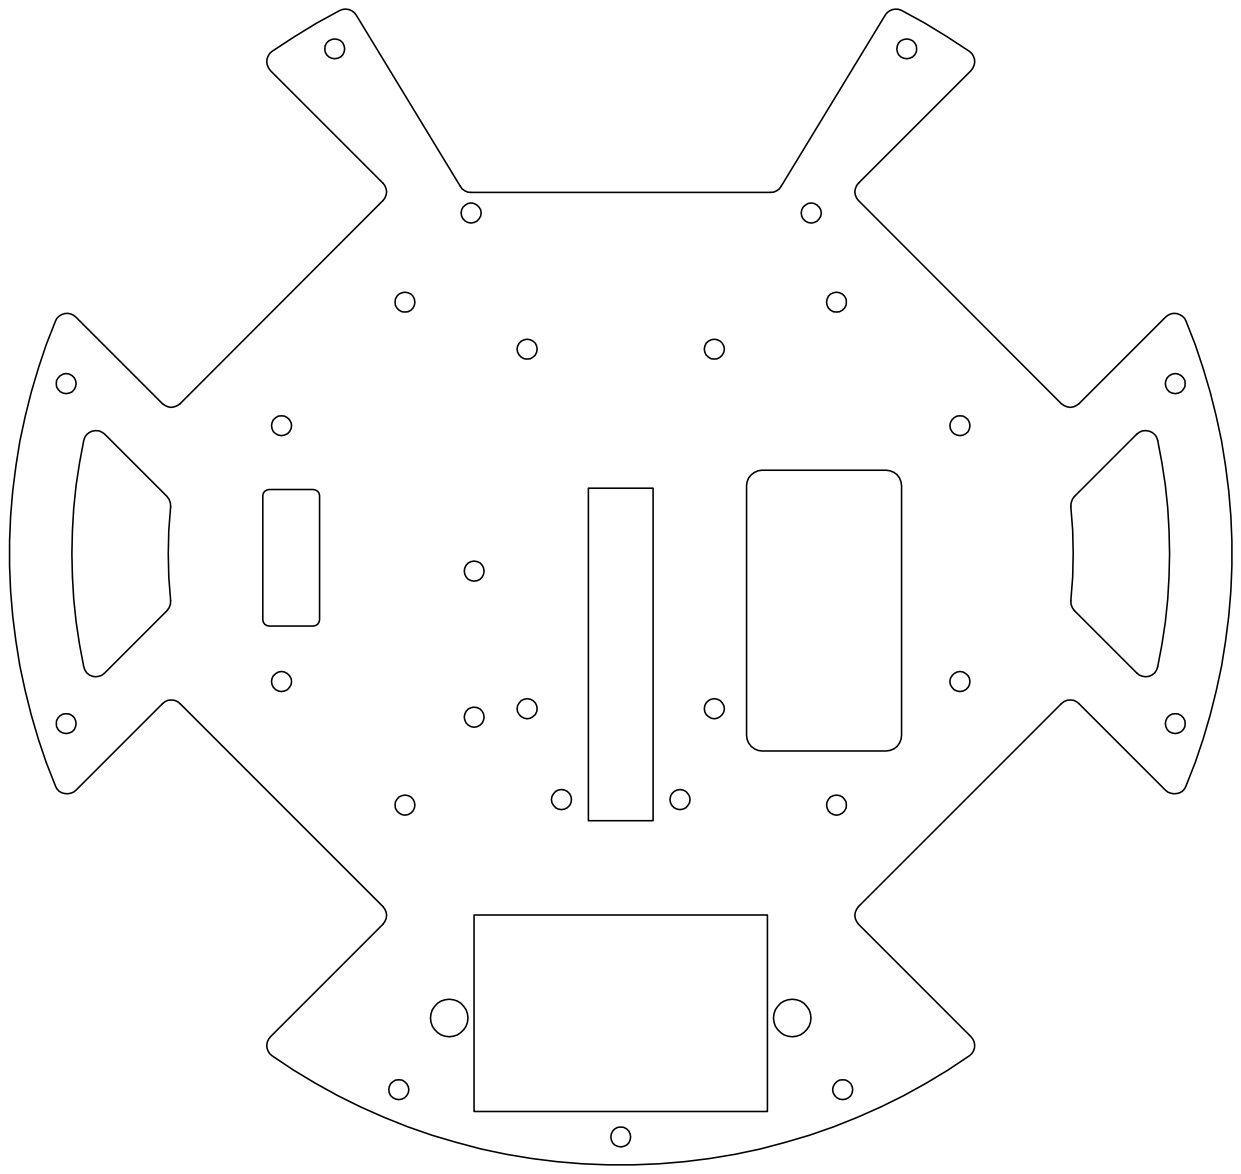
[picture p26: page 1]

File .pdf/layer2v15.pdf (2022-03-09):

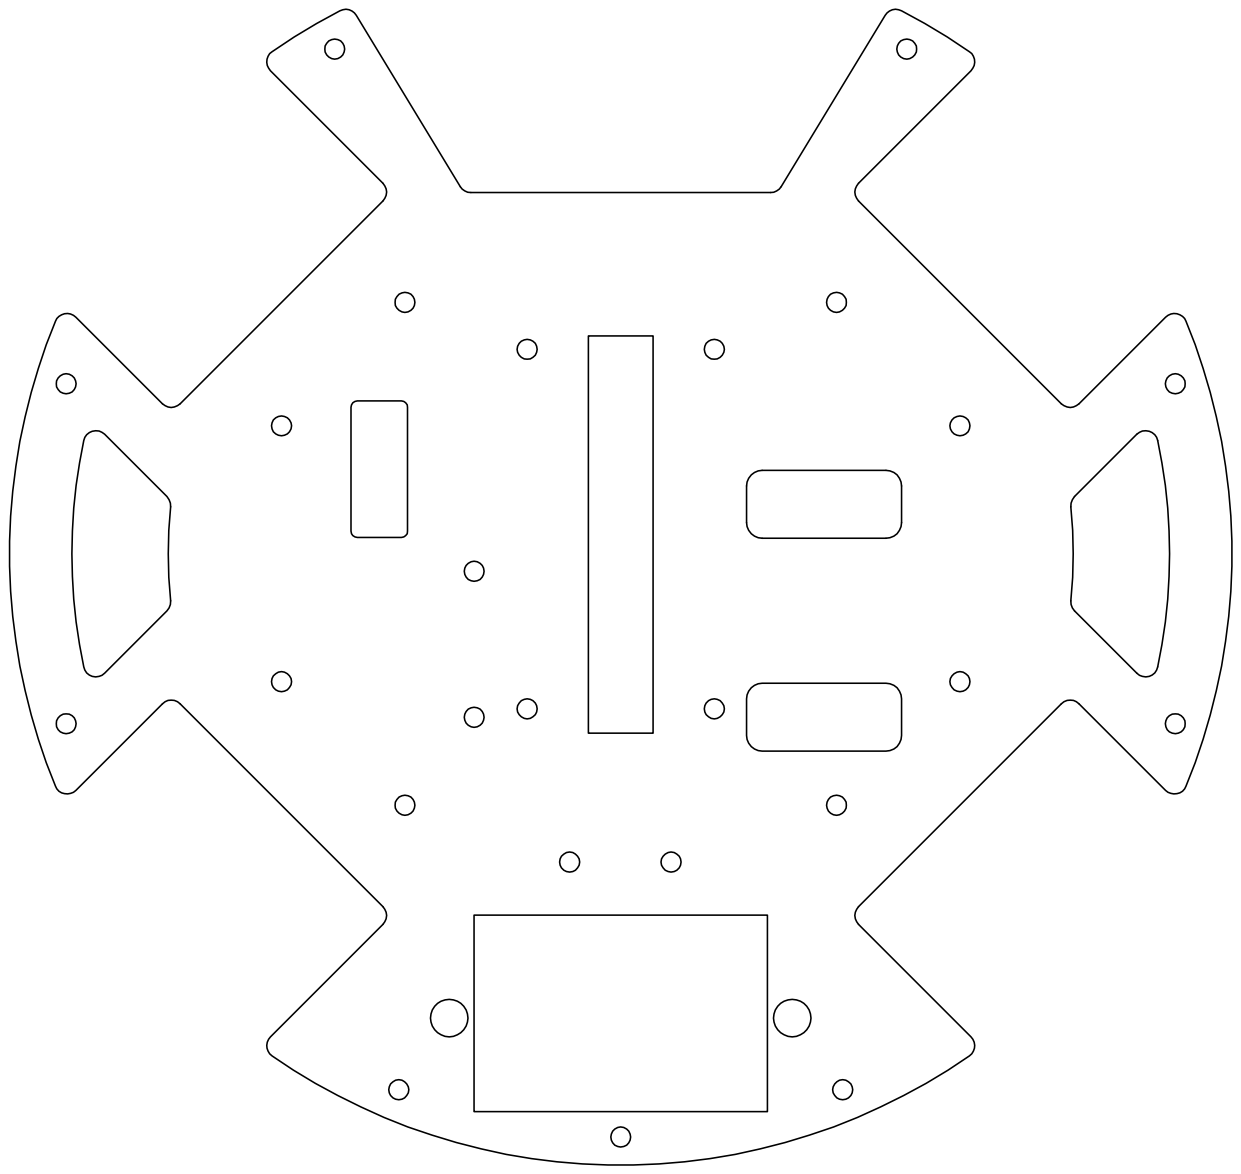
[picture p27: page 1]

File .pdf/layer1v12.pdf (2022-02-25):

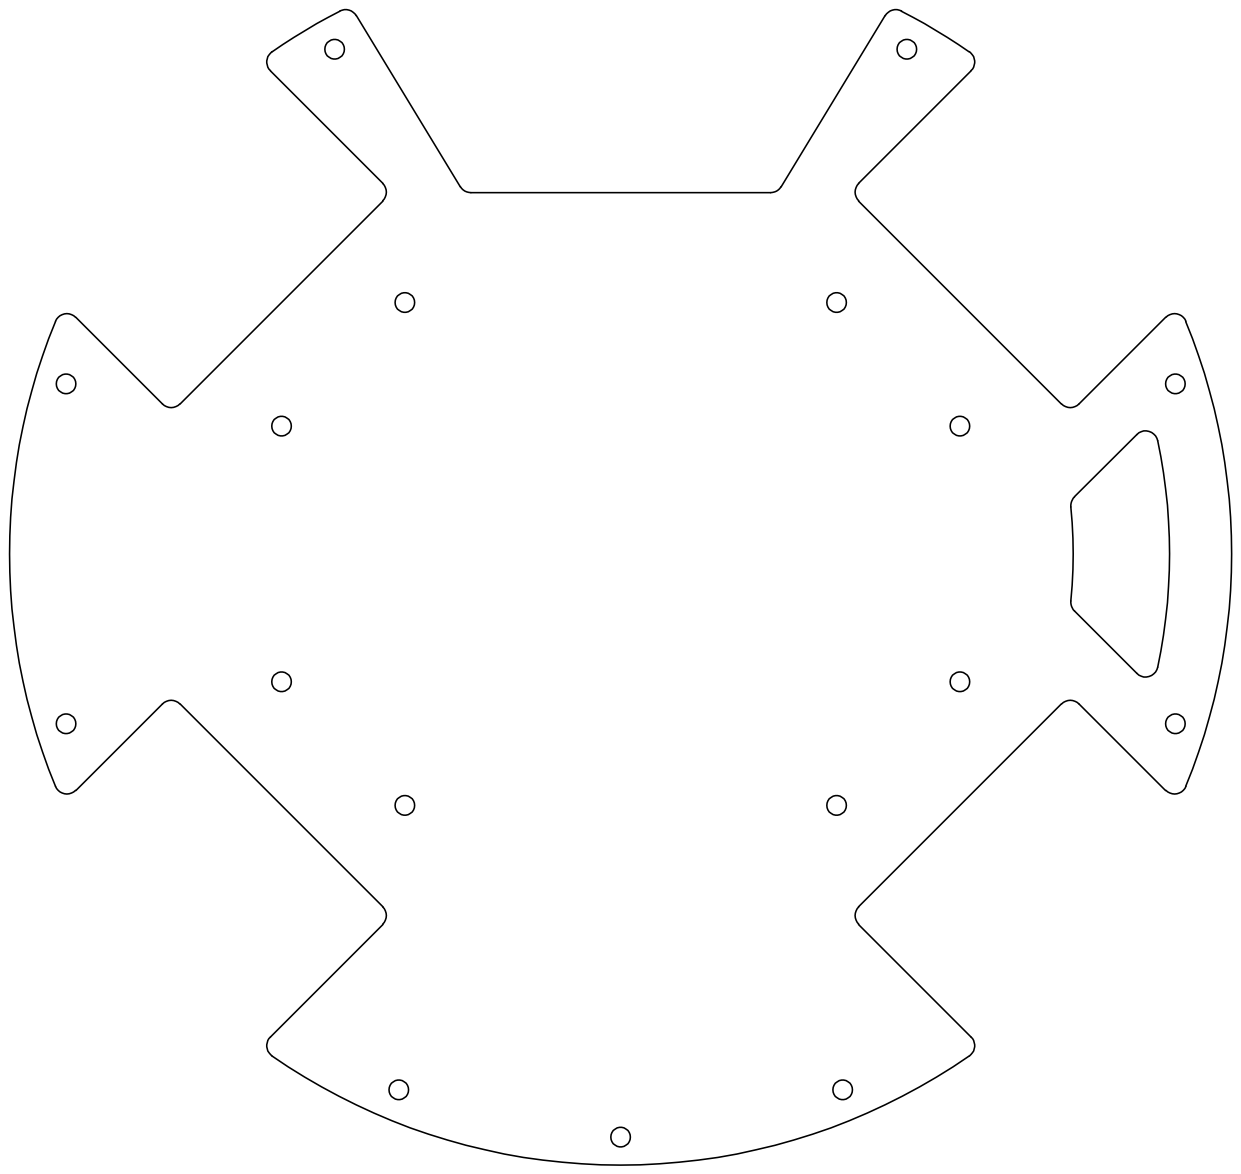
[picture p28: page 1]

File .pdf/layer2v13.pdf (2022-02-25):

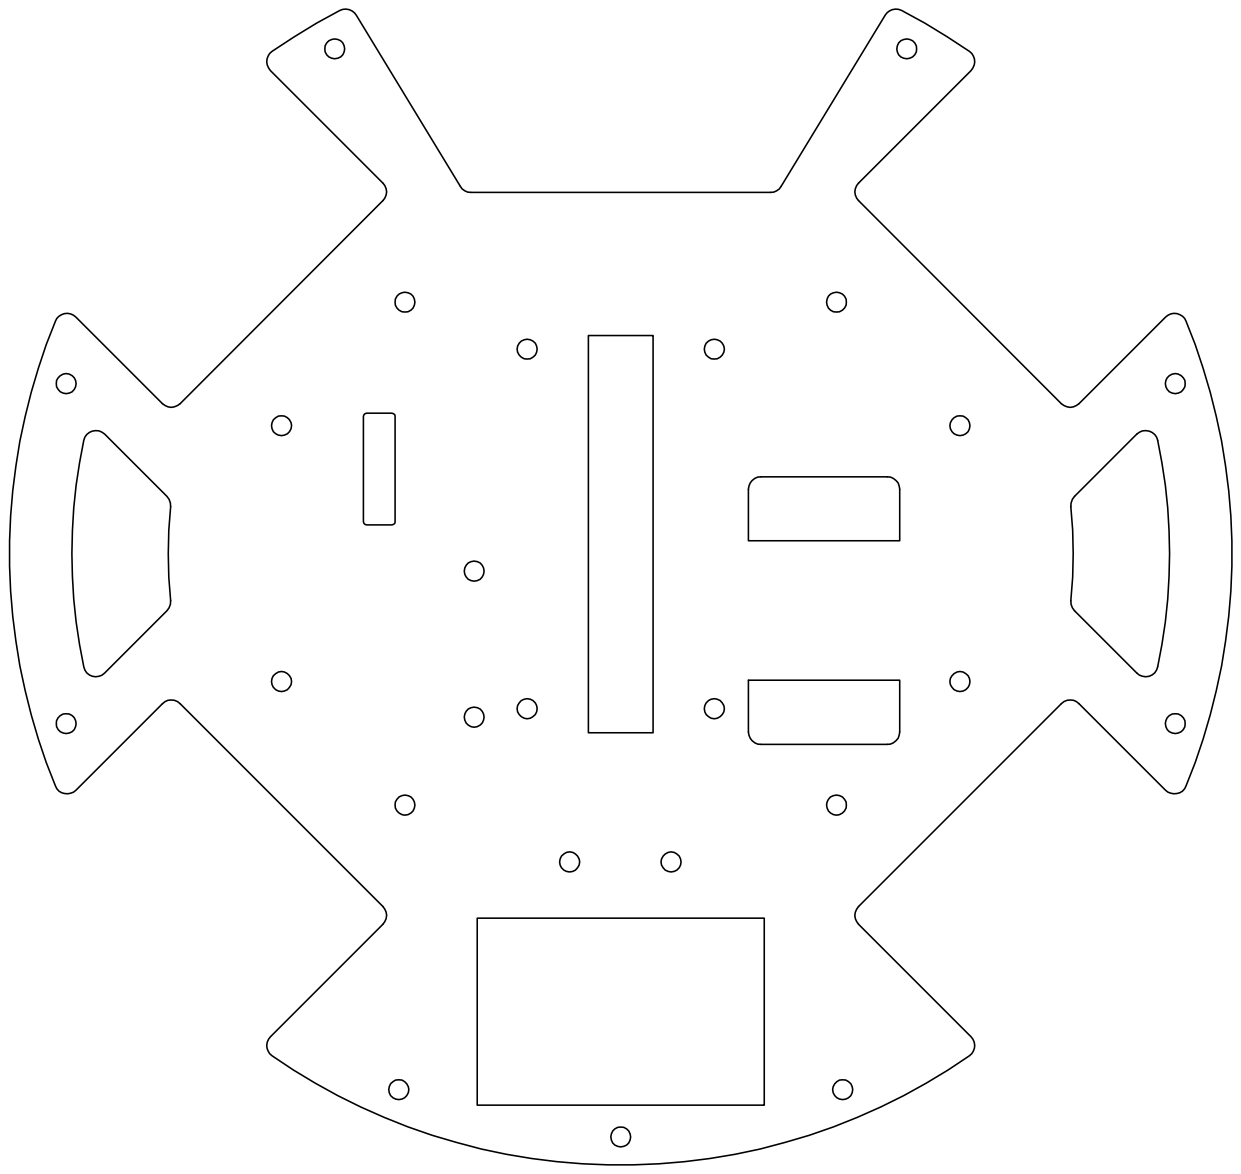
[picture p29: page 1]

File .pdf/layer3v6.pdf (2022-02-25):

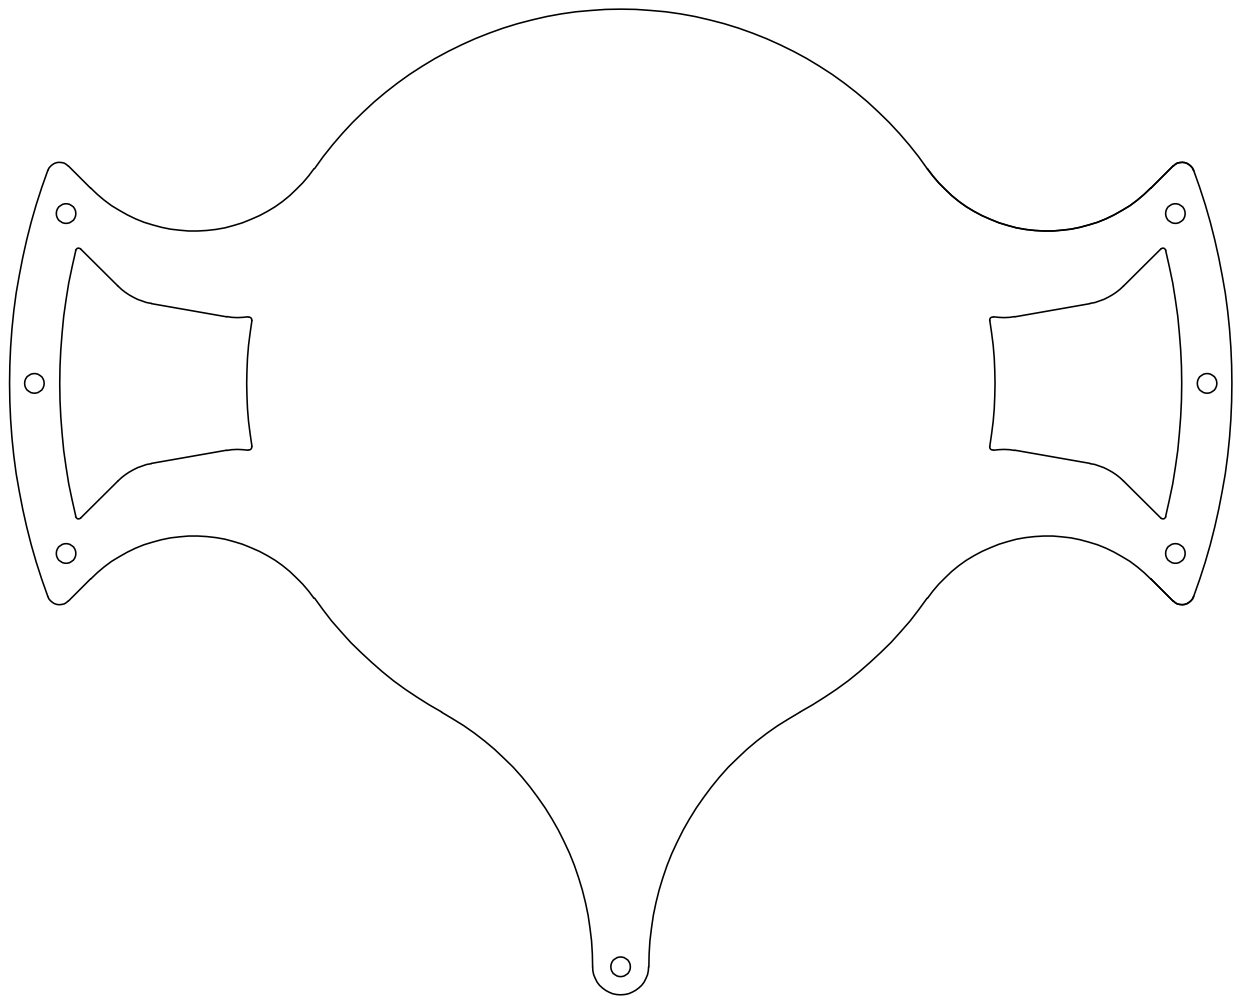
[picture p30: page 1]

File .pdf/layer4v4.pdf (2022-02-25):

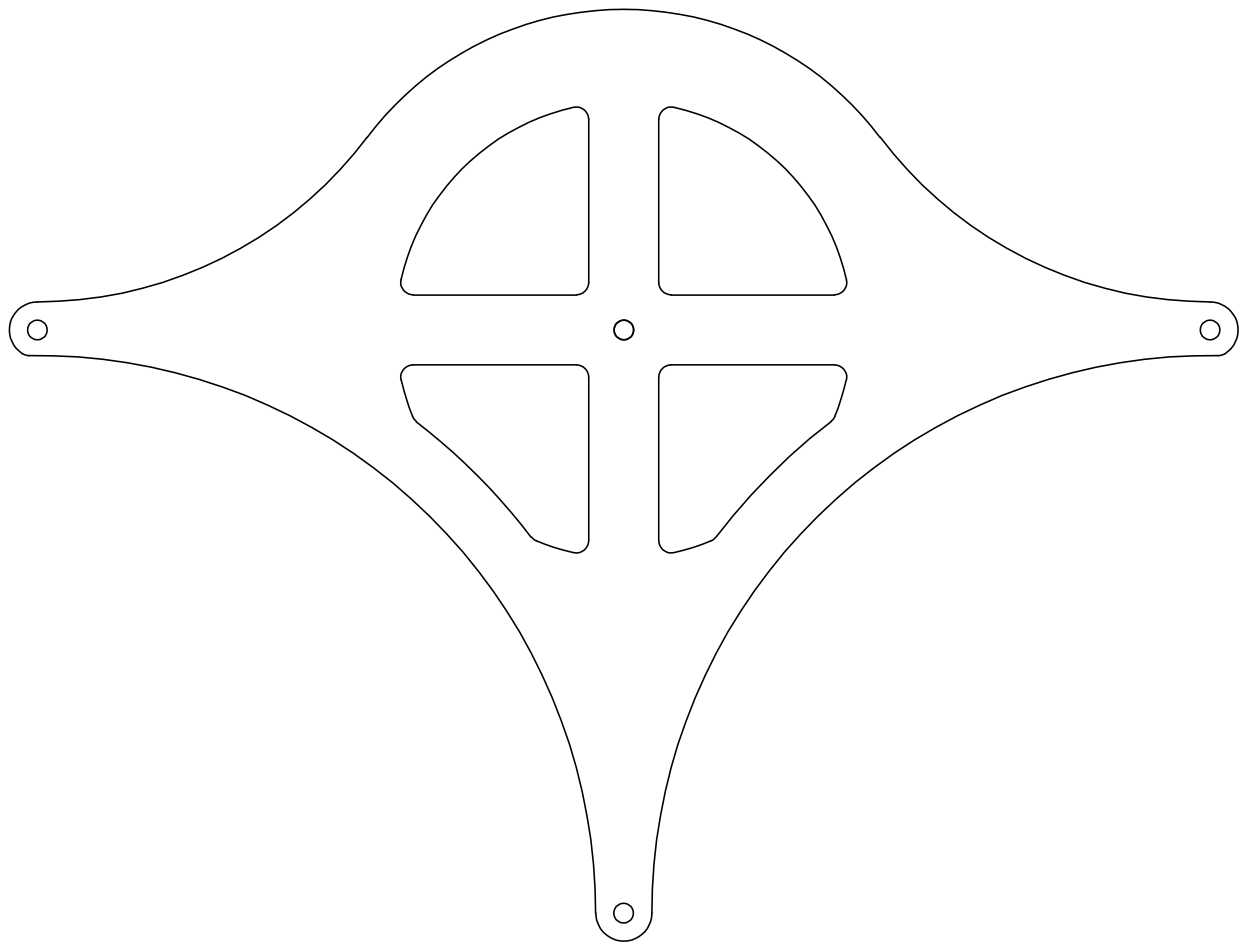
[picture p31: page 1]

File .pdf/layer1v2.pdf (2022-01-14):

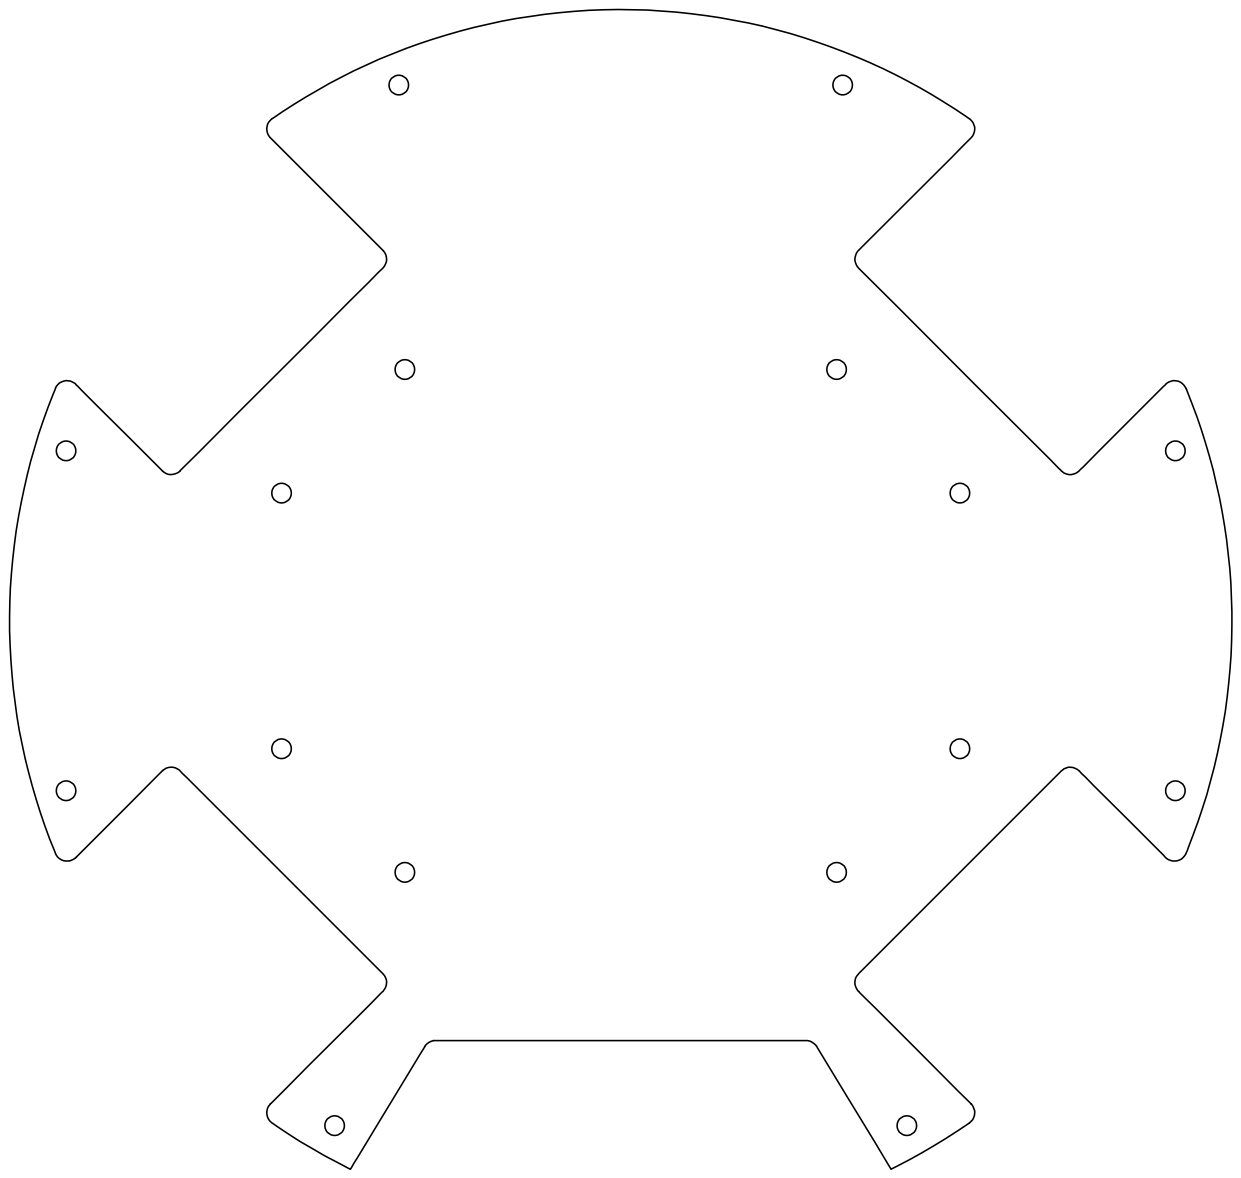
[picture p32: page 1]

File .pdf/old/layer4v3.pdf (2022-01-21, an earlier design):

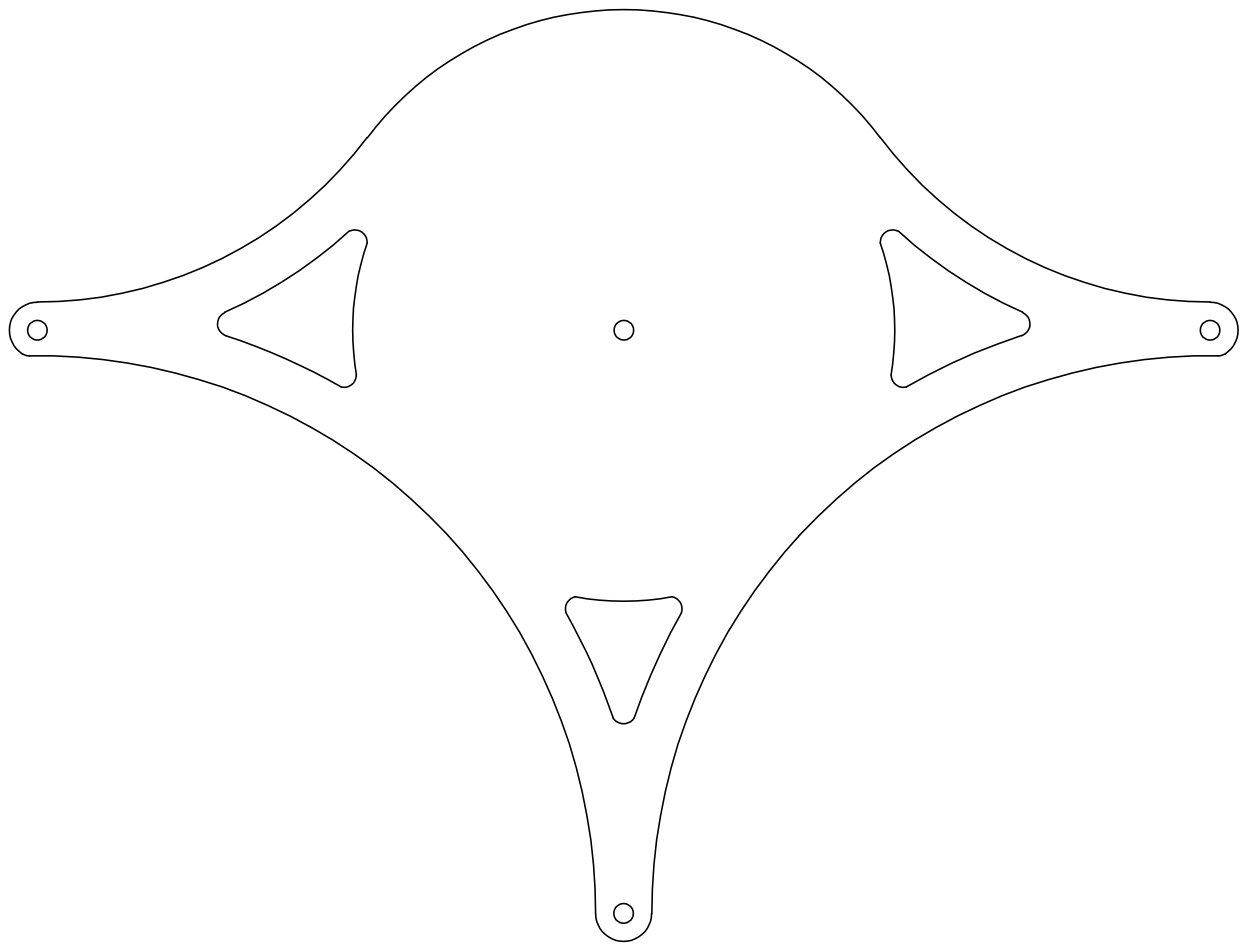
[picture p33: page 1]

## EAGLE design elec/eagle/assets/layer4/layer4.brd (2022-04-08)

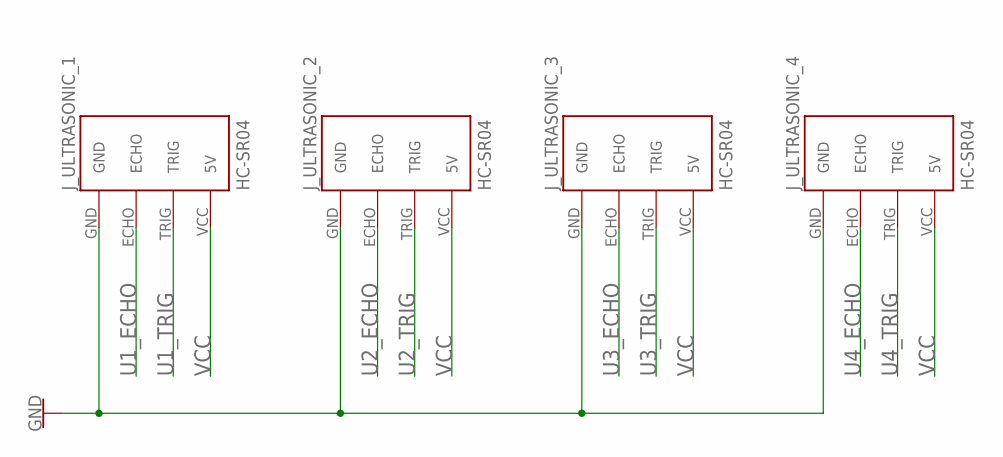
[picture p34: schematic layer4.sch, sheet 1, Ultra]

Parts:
J_ULTRASONIC_1, J_ULTRASONIC_2, J_ULTRASONIC_3, J_ULTRASONIC_4: HC-SR04; HC-SR04_FOOTPRINT

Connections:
GND: J_ULTRASONIC_1.GND, J_ULTRASONIC_2.GND, J_ULTRASONIC_3.GND, J_ULTRASONIC_4.GND; also elsewhere on the board
U1_ECHO: J_ULTRASONIC_1.ECHO; also elsewhere on the board
U1_TRIG: J_ULTRASONIC_1.TRIG; also elsewhere on the board
U2_ECHO: J_ULTRASONIC_2.ECHO; also elsewhere on the board
U2_TRIG: J_ULTRASONIC_2.TRIG; also elsewhere on the board
U3_ECHO: J_ULTRASONIC_3.ECHO; also elsewhere on the board
U3_TRIG: J_ULTRASONIC_3.TRIG; also elsewhere on the board
U4_ECHO: J_ULTRASONIC_4.ECHO; also elsewhere on the board
U4_TRIG: J_ULTRASONIC_4.TRIG; also elsewhere on the board
VCC: J_ULTRASONIC_1.VCC (5V), J_ULTRASONIC_2.VCC (5V), J_ULTRASONIC_3.VCC (5V), J_ULTRASONIC_4.VCC (5V); also elsewhere on the board

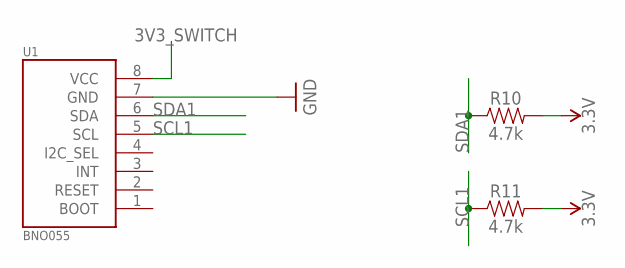
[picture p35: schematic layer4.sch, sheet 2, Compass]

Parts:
R10, R11: 4.7k; 0603
U1: BNO055

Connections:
3.3V: R10.2, R11.2
3V3_SWITCH: U1.8 (VCC); also elsewhere on the board
GND: U1.7 (GND); also elsewhere on the board
SCL1: R11.1, U1.5 (SCL); also elsewhere on the board
SDA1: R10.1, U1.6 (SDA); also elsewhere on the board

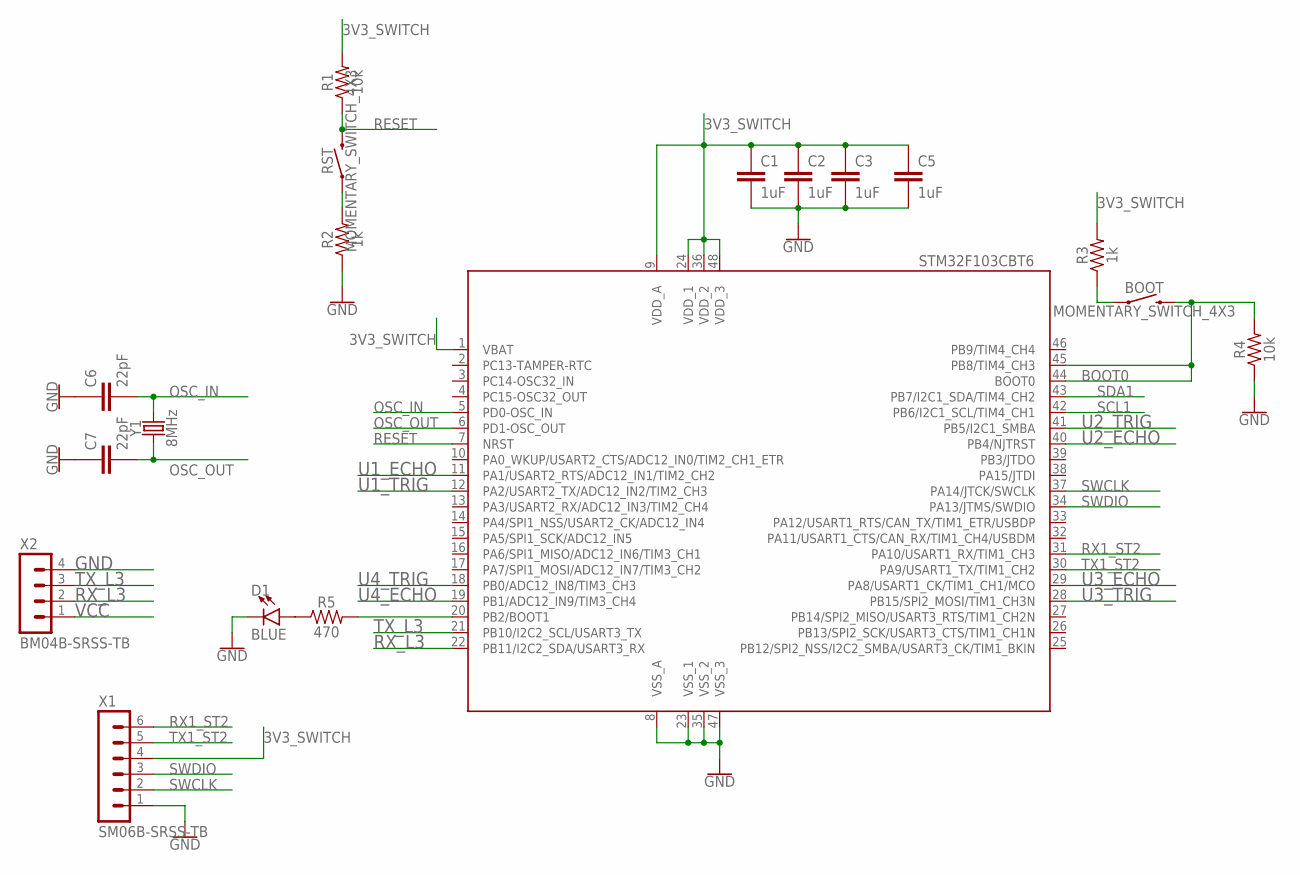
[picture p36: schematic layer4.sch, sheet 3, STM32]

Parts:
BOOT: MOMENTARY_SWITCH_4X3
C1, C2, C3, C5: 1uF; C0603
C6, C7: 22pF; C0603
D1: BLUE; LED-0603
R1, R4: 10k; R0603
R2, R3: 1k; R0603
R5: 470; R0603
RST: MOMENTARY_SWITCH_4X3
STM32_IR: STM32F103CBT6; LQFP48
X1: SM06B-SRSS-TB
X2: BM04B-SRSS-TB
Y1: 8MHz; CRYSTAL-SMD-5X3.2-2PAD

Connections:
3V3_SWITCH: C1.1, C2.1, C3.1, C5.2, R1.2, R3.2, STM32_IR.1 (VBAT), STM32_IR.9 (VDD_A), STM32_IR.24 (VDD_1), STM32_IR.36 (VDD_2), STM32_IR.48 (VDD_3), X1.4; also elsewhere on the board
BOOT0: BOOT.P$2 (2), R4.2, STM32_IR.44 (BOOT0), STM32_IR.45 (PB8/TIM4_CH3)
GND: C1.2, C2.2, C3.2, C5.1, C6.1, C7.1, D1.C, R2.1, R4.1, STM32_IR.8 (VSS_A), STM32_IR.23 (VSS_1), STM32_IR.35 (VSS_2), STM32_IR.47 (VSS_3), X1.1, X2.4; also elsewhere on the board
unnamed: R2.2, RST.P$1 (1)
unnamed: BOOT.P$1 (1), R3.1
unnamed: R5.2, STM32_IR.20 (PB2/BOOT1)
unnamed: D1.A, R5.1
OSC_IN: C6.2, STM32_IR.5 (PD0-OSC_IN), Y1.P$2 (2)
OSC_OUT: C7.2, STM32_IR.6 (PD1-OSC_OUT), Y1.P$1 (1)
RESET: R1.1, RST.P$2 (2), STM32_IR.7 (NRST)
RX1_ST2: STM32_IR.31 (PA10/USART1_RX/TIM1_CH3), X1.6
RX_L3: STM32_IR.22 (PB11/I2C2_SDA/USART3_RX), X2.2
SCL1: STM32_IR.42 (PB6/I2C1_SCL/TIM4_CH1); also elsewhere on the board
SDA1: STM32_IR.43 (PB7/I2C1_SDA/TIM4_CH2); also elsewhere on the board
SWCLK: STM32_IR.37 (PA14/JTCK/SWCLK), X1.2
SWDIO: STM32_IR.34 (PA13/JTMS/SWDIO), X1.3
TX1_ST2: STM32_IR.30 (PA9/USART1_TX/TIM1_CH2), X1.5
TX_L3: STM32_IR.21 (PB10/I2C2_SCL/USART3_TX), X2.3
U1_ECHO: STM32_IR.11 (PA1/USART2_RTS/ADC12_IN1/TIM2_CH2); also elsewhere on the board
U1_TRIG: STM32_IR.12 (PA2/USART2_TX/ADC12_IN2/TIM2_CH3); also elsewhere on the board
U2_ECHO: STM32_IR.40 (PB4/NJTRST); also elsewhere on the board
U2_TRIG: STM32_IR.41 (PB5/I2C1_SMBA); also elsewhere on the board
U3_ECHO: STM32_IR.29 (PA8/USART1_CK/TIM1_CH1/MCO); also elsewhere on the board
U3_TRIG: STM32_IR.28 (PB15/SPI2_MOSI/TIM1_CH3N); also elsewhere on the board
U4_ECHO: STM32_IR.19 (PB1/ADC12_IN9/TIM3_CH4); also elsewhere on the board
U4_TRIG: STM32_IR.18 (PB0/ADC12_IN8/TIM3_CH3); also elsewhere on the board
VCC: X2.1; also elsewhere on the board

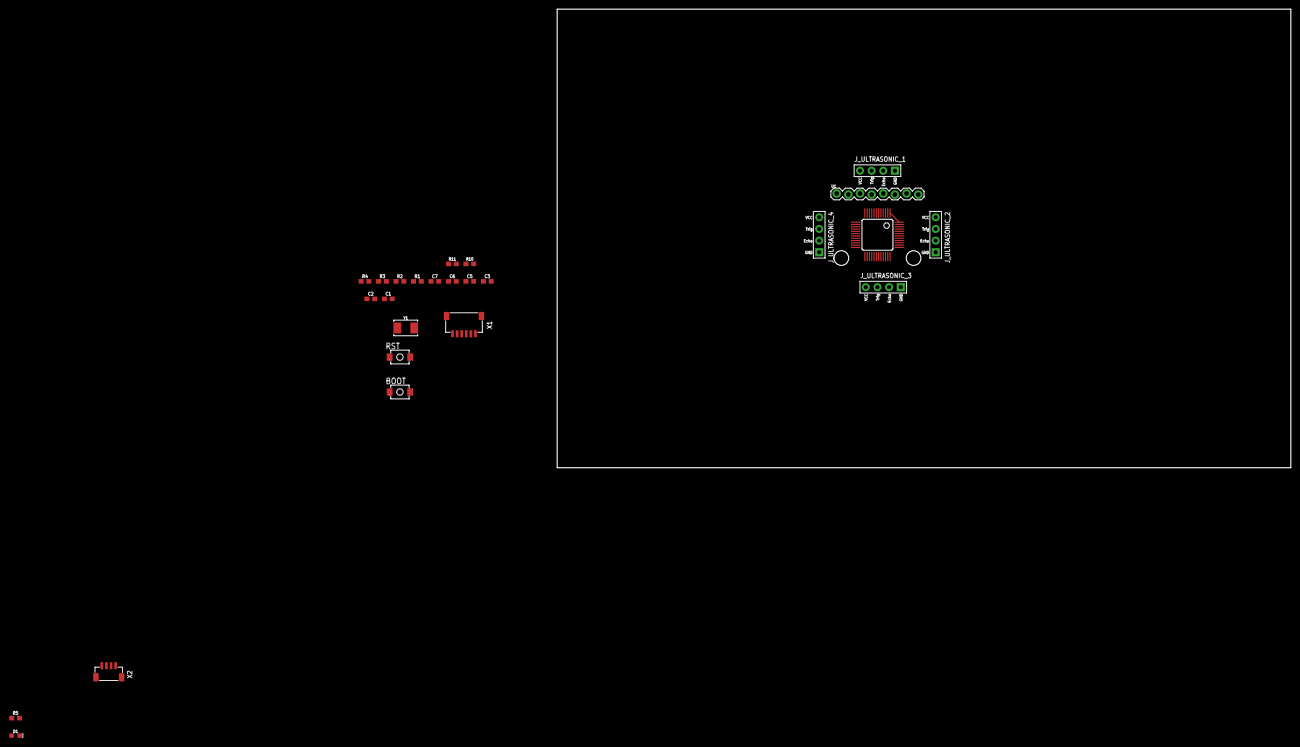
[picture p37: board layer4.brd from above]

Board: 2 copper layers, 160.0 x 100.0 mm, 25 parts (0 on the bottom side), 28 nets.

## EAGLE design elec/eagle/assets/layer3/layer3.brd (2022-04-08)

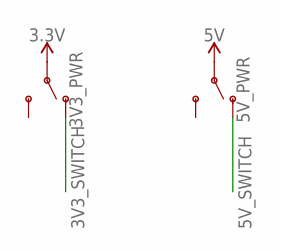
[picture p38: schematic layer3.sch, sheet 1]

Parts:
3V3_PWR, 5V_PWR: SWITCH-SPDT-PTH-11.6X4.0MM-LOCK; SWITCH_SPDT_PTH_11.6X4.0MM_LOCK

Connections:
3.3V: 3V3_PWR.2; also elsewhere on the board
3V3_SWITCH: 3V3_PWR.1 (O); also elsewhere on the board
5V: 5V_PWR.2; also elsewhere on the board
5V_SWITCH: 5V_PWR.1 (O); also elsewhere on the board

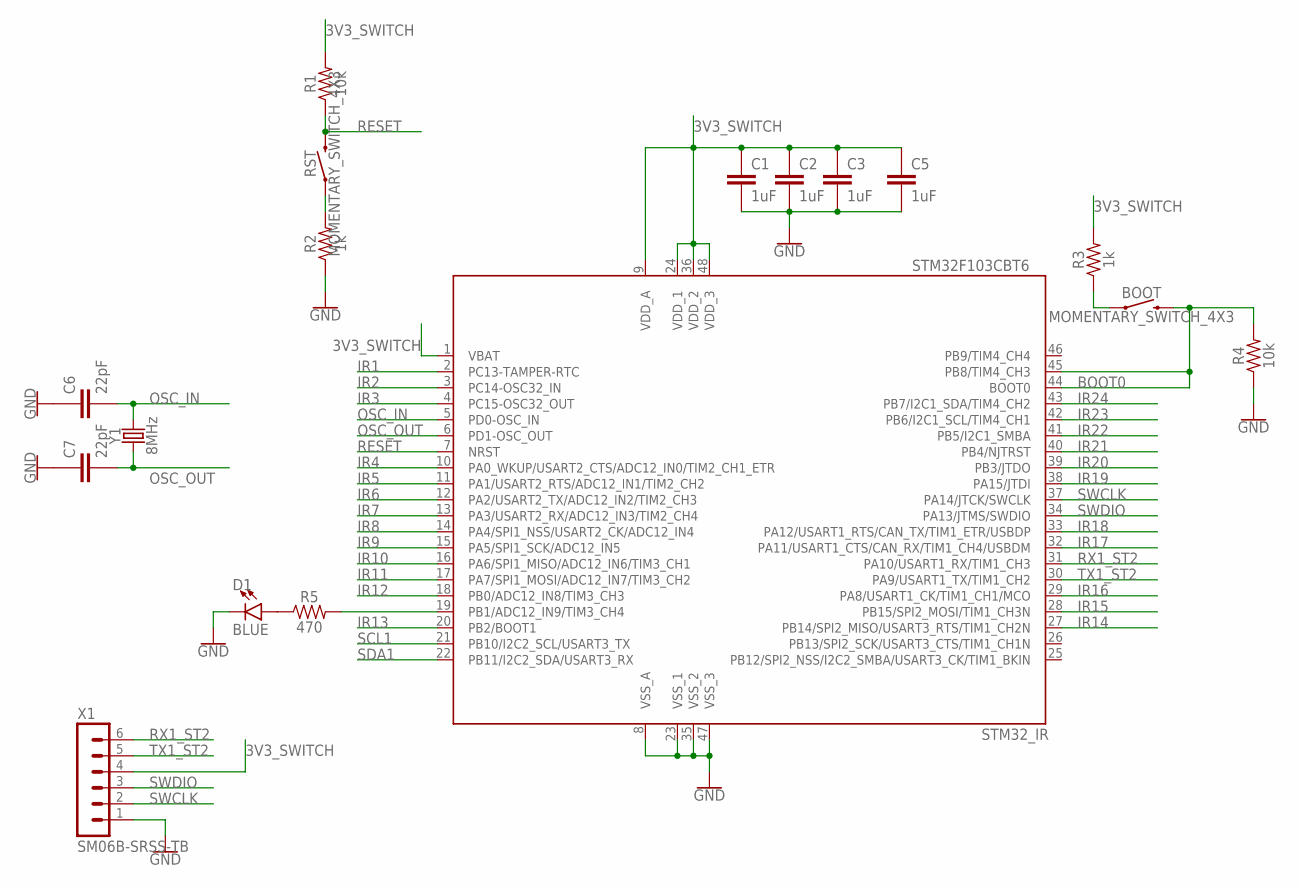
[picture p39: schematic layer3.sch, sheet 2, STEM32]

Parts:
BOOT: MOMENTARY_SWITCH_4X3
C1, C2, C3, C5: 1uF; C0603
C6, C7: 22pF; C0603
D1: BLUE; LED-0603
R1, R4: 10k; R0603
R2, R3: 1k; R0603
R5: 470; R0603
RST: MOMENTARY_SWITCH_4X3
STM32_IR: STM32F103CBT6; LQFP48
X1: SM06B-SRSS-TB
Y1: 8MHz; CRYSTAL-SMD-5X3.2-2PAD

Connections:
3V3_SWITCH: C1.1, C2.1, C3.1, C5.2, R1.2, R3.2, STM32_IR.1 (VBAT), STM32_IR.9 (VDD_A), STM32_IR.24 (VDD_1), STM32_IR.36 (VDD_2), STM32_IR.48 (VDD_3), X1.4; also elsewhere on the board
BOOT0: BOOT.P$2 (2), R4.2, STM32_IR.44 (BOOT0), STM32_IR.45 (PB8/TIM4_CH3)
GND: C1.2, C2.2, C3.2, C5.1, C6.1, C7.1, D1.C, R2.1, R4.1, STM32_IR.8 (VSS_A), STM32_IR.23 (VSS_1), STM32_IR.35 (VSS_2), STM32_IR.47 (VSS_3), X1.1; also elsewhere on the board
IR1: STM32_IR.2 (PC13-TAMPER-RTC); also elsewhere on the board
IR2: STM32_IR.3 (PC14-OSC32_IN); also elsewhere on the board
IR3: STM32_IR.4 (PC15-OSC32_OUT); also elsewhere on the board
IR4: STM32_IR.10 (PA0_WKUP/USART2_CTS/ADC12_IN0/TIM2_CH1_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); also elsewhere on the board
IR5: STM32_IR.11 (PA1/USART2_RTS/ADC12_IN1/TIM2_CH2); also elsewhere on the board
IR6: STM32_IR.12 (PA2/USART2_TX/ADC12_IN2/TIM2_CH3); also elsewhere on the board
IR7: STM32_IR.13 (PA3/USART2_RX/ADC12_IN3/TIM2_CH4); also elsewhere on the board
IR8: STM32_IR.14 (PA4/SPI1_NSS/USART2_CK/ADC12_IN4); also elsewhere on the board
IR9: STM32_IR.15 (PA5/SPI1_SCK/ADC12_IN5); also elsewhere on the board
IR10: STM32_IR.16 (PA6/SPI1_MISO/ADC12_IN6/TIM3_CH1); also elsewhere on the board
IR11: STM32_IR.17 (PA7/SPI1_MOSI/ADC12_IN7/TIM3_CH2); also elsewhere on the board
IR12: STM32_IR.18 (PB0/ADC12_IN8/TIM3_CH3); also elsewhere on the board
IR13: STM32_IR.20 (PB2/BOOT1); also elsewhere on the board
IR14: STM32_IR.27 (PB14/SPI2_MISO/USART3_RTS/TIM1_CH2N); also elsewhere on the board
IR15: STM32_IR.28 (PB15/SPI2_MOSI/TIM1_CH3N); also elsewhere on the board
IR16: STM32_IR.29 (PA8/USART1_CK/TIM1_CH1/MCO); also elsewhere on the board
IR17: STM32_IR.32 (PA11/USART1_CTS/CAN_RX/TIM1_CH4/USBDM); also elsewhere on the board
IR18: STM32_IR.33 (PA12/USART1_RTS/CAN_TX/TIM1_ETR/USBDP); also elsewhere on the board
IR19: STM32_IR.38 (PA15/JTDI); also elsewhere on the board
IR20: STM32_IR.39 (PB3/JTDO); also elsewhere on the board
IR21: STM32_IR.40 (PB4/NJTRST); also elsewhere on the board
IR22: STM32_IR.41 (PB5/I2C1_SMBA); also elsewhere on the board
IR23: STM32_IR.42 (PB6/I2C1_SCL/TIM4_CH1); also elsewhere on the board
IR24: STM32_IR.43 (PB7/I2C1_SDA/TIM4_CH2); also elsewhere on the board
unnamed: R2.2, RST.P$1 (1)
unnamed: BOOT.P$1 (1), R3.1
unnamed: R5.2, STM32_IR.19 (PB1/ADC12_IN9/TIM3_CH4)
unnamed: D1.A, R5.1
OSC_IN: C6.2, STM32_IR.5 (PD0-OSC_IN), Y1.P$2 (2)
OSC_OUT: C7.2, STM32_IR.6 (PD1-OSC_OUT), Y1.P$1 (1)
RESET: R1.1, RST.P$2 (2), STM32_IR.7 (NRST)
RX1_ST2: STM32_IR.31 (PA10/USART1_RX/TIM1_CH3), X1.6; also elsewhere on the board
SCL1: STM32_IR.21 (PB10/I2C2_SCL/USART3_TX)
SDA1: STM32_IR.22 (PB11/I2C2_SDA/USART3_RX)
SWCLK: STM32_IR.37 (PA14/JTCK/SWCLK), X1.2
SWDIO: STM32_IR.34 (PA13/JTMS/SWDIO), X1.3
TX1_ST2: STM32_IR.30 (PA9/USART1_TX/TIM1_CH2), X1.5; also elsewhere on the board

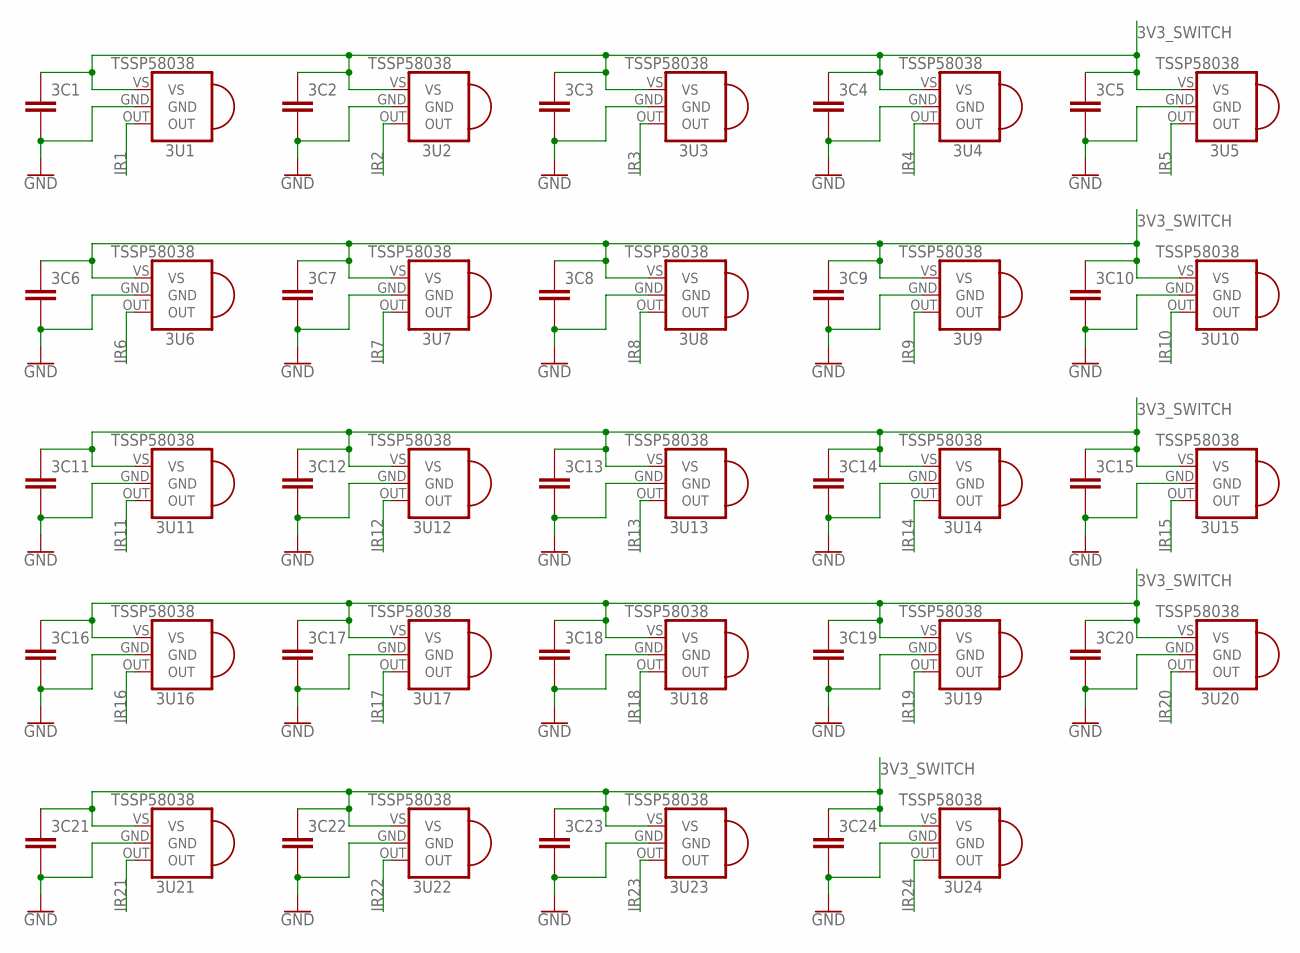
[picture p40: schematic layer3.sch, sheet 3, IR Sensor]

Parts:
3C1, 3C2, 3C3, 3C4, 3C5, 3C6, 3C7, 3C8, 3C9, 3C10, 3C11, 3C12, 3C13, 3C14, 3C15, 3C16, 3C17, 3C18, 3C19, 3C20, 3C21, 3C22, 3C23, 3C24: CAPACITOR0603; C0603
3U1, 3U2, 3U3, 3U4, 3U5, 3U6, 3U7, 3U8, 3U9, 3U10, 3U11, 3U12, 3U13, 3U14, 3U15, 3U16, 3U17, 3U18, 3U19, 3U20, 3U21, 3U22, 3U23, 3U24: TSSP58038

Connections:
3V3_SWITCH: 3C1.1, 3C2.1, 3C3.1, 3C4.1, 3C5.1, 3C6.1, 3C7.1, 3C8.1, 3C9.1, 3C10.1, 3C11.1, 3C12.1, 3C13.1, 3C14.1, 3C15.1, 3C16.1, 3C17.1, 3C18.1, 3C19.1, 3C20.1, 3C21.1, 3C22.1, 3C23.1, 3C24.1, 3U1.VS, 3U2.VS, 3U3.VS, 3U4.VS, 3U5.VS, 3U6.VS, 3U7.VS, 3U8.VS, 3U9.VS, 3U10.VS, 3U11.VS, 3U12.VS, 3U13.VS, 3U14.VS, 3U15.VS, 3U16.VS, 3U17.VS, 3U18.VS, 3U19.VS, 3U20.VS, 3U21.VS, 3U22.VS, 3U23.VS, 3U24.VS; also elsewhere on the board
GND: 3C1.2, 3C2.2, 3C3.2, 3C4.2, 3C5.2, 3C6.2, 3C7.2, 3C8.2, 3C9.2, 3C10.2, 3C11.2, 3C12.2, 3C13.2, 3C14.2, 3C15.2, 3C16.2, 3C17.2, 3C18.2, 3C19.2, 3C20.2, 3C21.2, 3C22.2, 3C23.2, 3C24.2, 3U1.GND, 3U2.GND, 3U3.GND, 3U4.GND, 3U5.GND, 3U6.GND, 3U7.GND, 3U8.GND, 3U9.GND, 3U10.GND, 3U11.GND, 3U12.GND, 3U13.GND, 3U14.GND, 3U15.GND, 3U16.GND, 3U17.GND, 3U18.GND, 3U19.GND, 3U20.GND, 3U21.GND, 3U22.GND, 3U23.GND, 3U24.GND; also elsewhere on the board
IR1: 3U1.OUT; also elsewhere on the board
IR2: 3U2.OUT; also elsewhere on the board
IR3: 3U3.OUT; also elsewhere on the board
IR4: 3U4.OUT; also elsewhere on the board
IR5: 3U5.OUT; also elsewhere on the board
IR6: 3U6.OUT; also elsewhere on the board
IR7: 3U7.OUT; also elsewhere on the board
IR8: 3U8.OUT; also elsewhere on the board
IR9: 3U9.OUT; also elsewhere on the board
IR10: 3U10.OUT; also elsewhere on the board
IR11: 3U11.OUT; also elsewhere on the board
IR12: 3U12.OUT; also elsewhere on the board
IR13: 3U13.OUT; also elsewhere on the board
IR14: 3U14.OUT; also elsewhere on the board
IR15: 3U15.OUT; also elsewhere on the board
IR16: 3U16.OUT; also elsewhere on the board
IR17: 3U17.OUT; also elsewhere on the board
IR18: 3U18.OUT; also elsewhere on the board
IR19: 3U19.OUT; also elsewhere on the board
IR20: 3U20.OUT; also elsewhere on the board
IR21: 3U21.OUT; also elsewhere on the board
IR22: 3U22.OUT; also elsewhere on the board
IR23: 3U23.OUT; also elsewhere on the board
IR24: 3U24.OUT; also elsewhere on the board

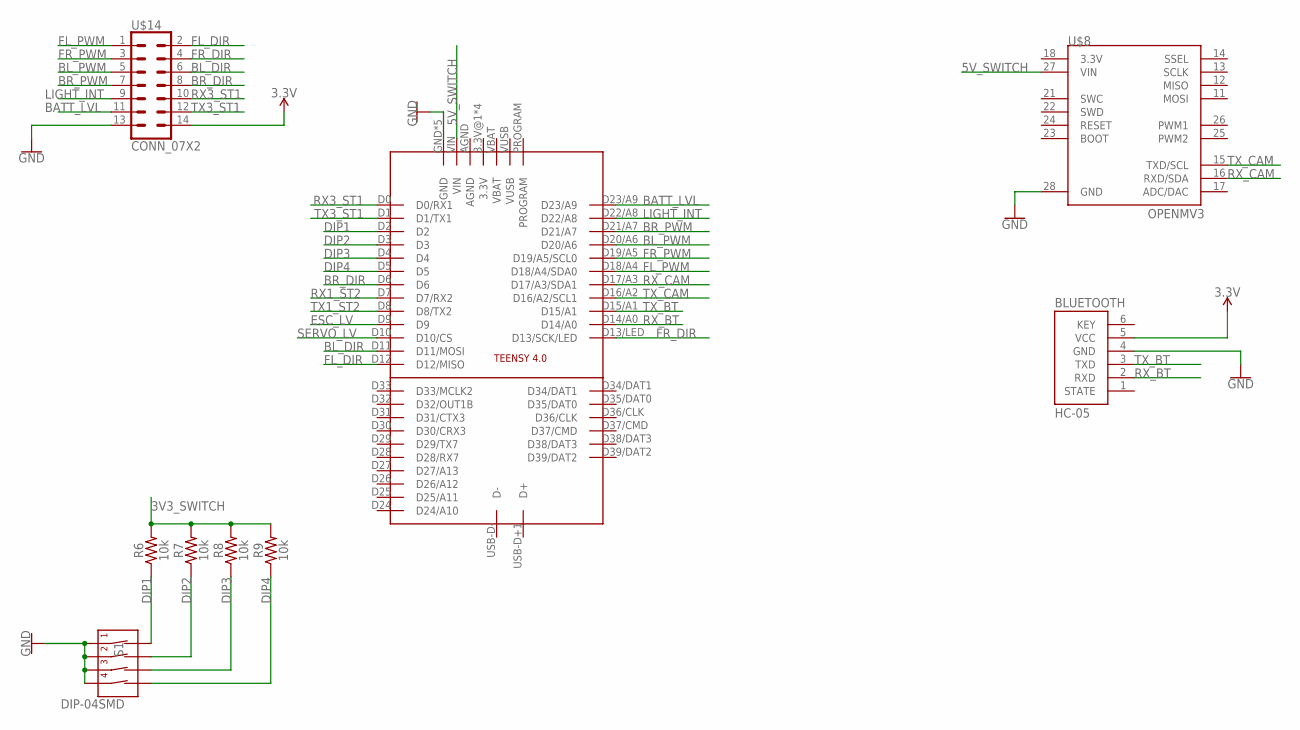
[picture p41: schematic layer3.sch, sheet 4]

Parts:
BLUETOOTH: HC-05
R6, R7, R8, R9: 10k; R0603
S1: DIP-04SMD; DIPSWITCH-04-SMD
TEENSY4: TEENSY-4.0-FULL-BREAKOUT-PINS
U$8: OPENMV3
U$14: CONN_07X2; 2X7

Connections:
3.3V: BLUETOOTH.5 (VCC), U$14.14; also elsewhere on the board
3V3_SWITCH: R6.2, R7.2, R8.2, R9.2; also elsewhere on the board
5V_SWITCH: TEENSY4.VIN, U$8.27 (VIN); also elsewhere on the board
BATT_LVL: TEENSY4.D23/A9, U$14.11
BL_DIR: TEENSY4.D11 (D11/MOSI), U$14.6
BL_PWM: TEENSY4.D20/A6, U$14.5
BR_DIR: TEENSY4.D6, U$14.8
BR_PWM: TEENSY4.D21/A7, U$14.7
DIP1: R6.1, S1.1 (1A), TEENSY4.D2
DIP2: R7.1, S1.2 (2A), TEENSY4.D3
DIP3: R8.1, S1.3 (3A), TEENSY4.D4
DIP4: R9.1, S1.4 (4A), TEENSY4.D5
ESC_LV: TEENSY4.D9; also elsewhere on the board
FL_DIR: TEENSY4.D12 (D12/MISO), U$14.2
FL_PWM: TEENSY4.D18/A4 (D18/A4/SDA0), U$14.1
FR_DIR: TEENSY4.D13/LED (D13/SCK/LED), U$14.4
FR_PWM: TEENSY4.D19/A5 (D19/A5/SCL0), U$14.3
GND: BLUETOOTH.4 (GND), S1.5 (4B), S1.6 (3B), S1.7 (2B), S1.8 (1B), TEENSY4.GND, TEENSY4.GND@1 (GND), TEENSY4.GND@2 (GND), TEENSY4.P$11 (GND), TEENSY4.P$12 (GND), U$8.28 (GND), U$14.13; also elsewhere on the board
LIGHT_INT: TEENSY4.D22/A8, U$14.9
RX1_ST2: TEENSY4.D7 (D7/RX2); also elsewhere on the board
RX3_ST1: TEENSY4.D0 (D0/RX1), U$14.10
RX_BT: BLUETOOTH.2 (RXD), TEENSY4.D14/A0
RX_CAM: TEENSY4.D17/A3 (D17/A3/SDA1), U$8.16 (RXD/SDA)
SERVO_LV: TEENSY4.D10 (D10/CS); also elsewhere on the board
TX1_ST2: TEENSY4.D8 (D8/TX2); also elsewhere on the board
TX3_ST1: TEENSY4.D1 (D1/TX1), U$14.12
TX_BT: BLUETOOTH.3 (TXD), TEENSY4.D15/A1
TX_CAM: TEENSY4.D16/A2 (D16/A2/SCL1), U$8.15 (TXD/SCL)

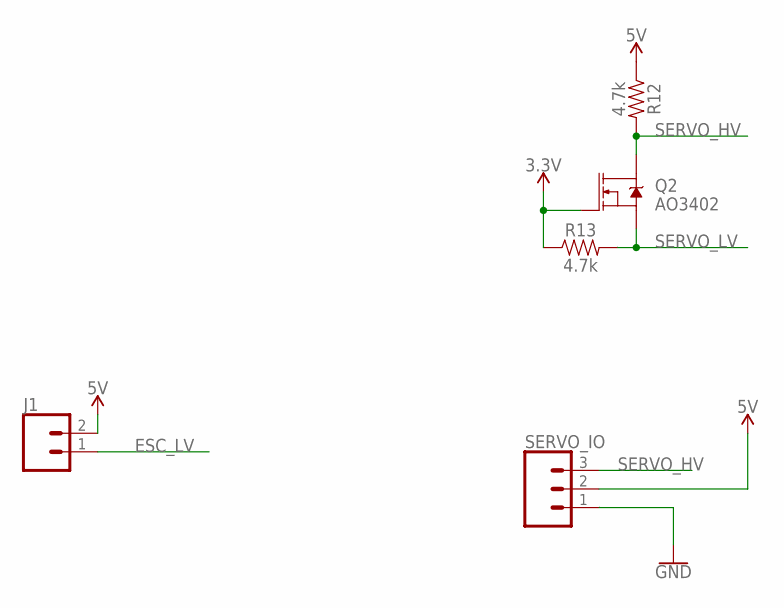
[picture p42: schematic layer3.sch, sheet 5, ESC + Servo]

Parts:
J1: CONN_02LOCK; 1X02_LOCK
Q2: AO3402; SOT23-3
R12, R13: 4.7k; R0603
SERVO_IO: CONN_03LOCK; 1X03_LOCK

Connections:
3.3V: Q2.1 (G), R13.1; also elsewhere on the board
5V: J1.2, R12.1, SERVO_IO.2; also elsewhere on the board
ESC_LV: J1.1; also elsewhere on the board
GND: SERVO_IO.1; also elsewhere on the board
SERVO_HV: Q2.3 (D), R12.2, SERVO_IO.3
SERVO_LV: Q2.2 (S), R13.2; also elsewhere on the board

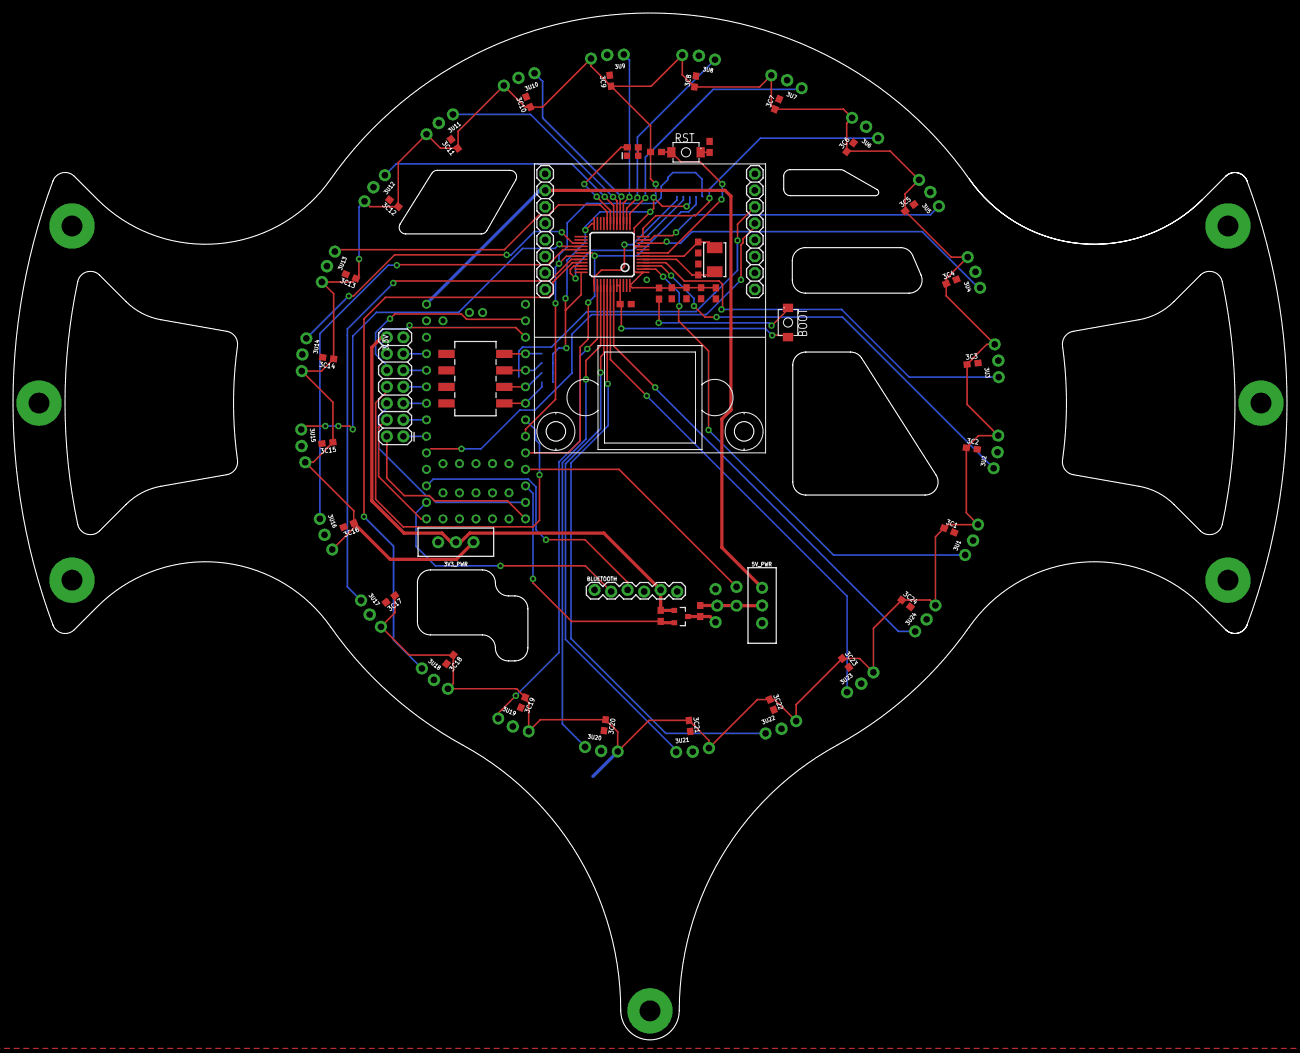
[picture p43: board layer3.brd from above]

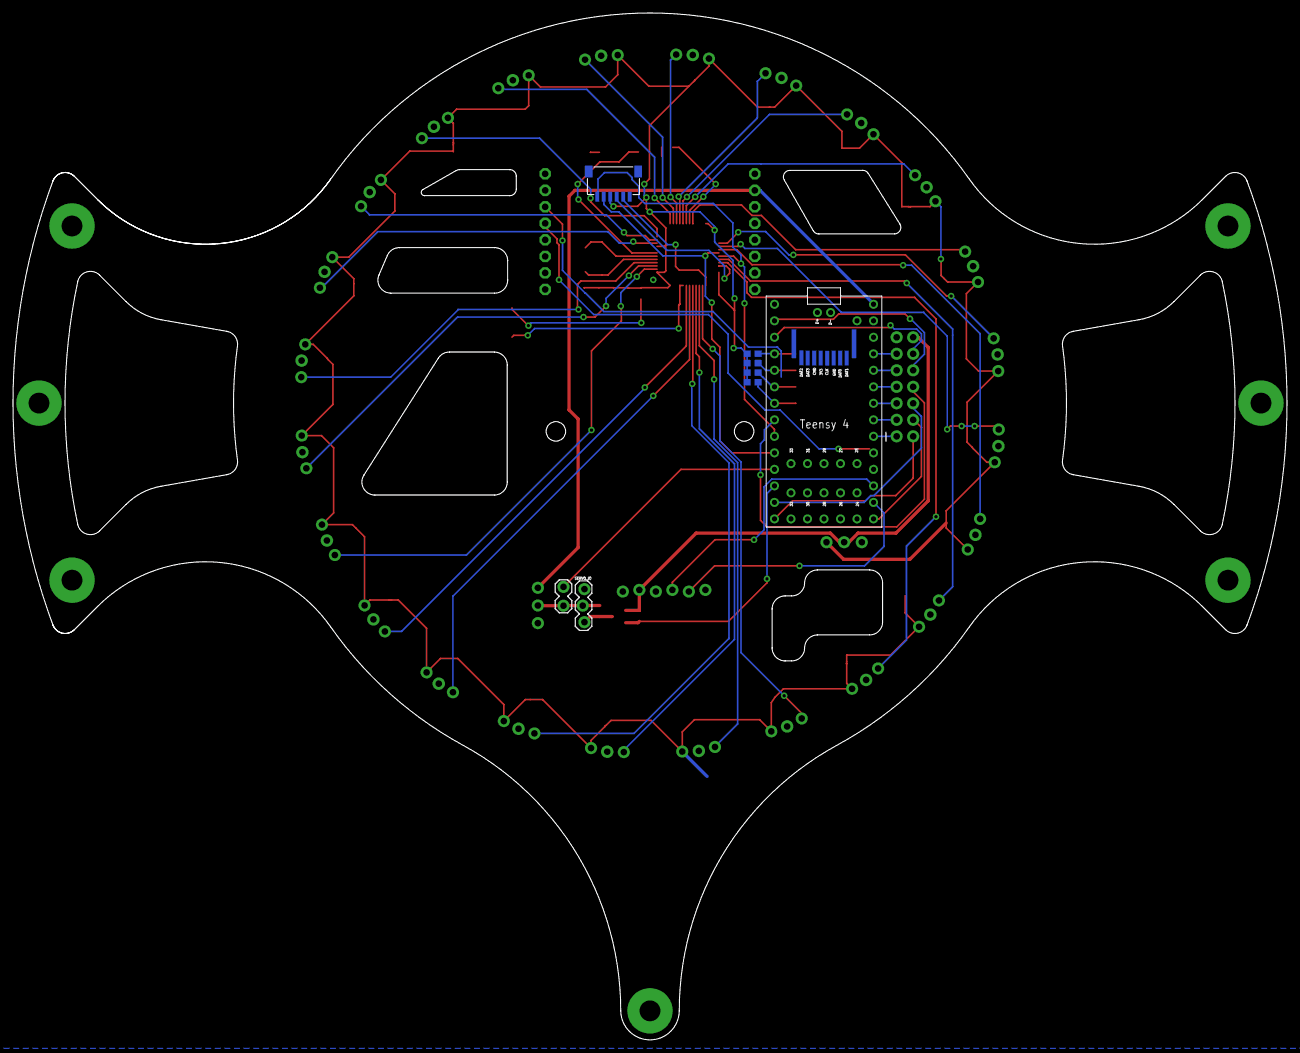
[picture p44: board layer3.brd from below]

Board: 2 copper layers, 196.0 x 158.0 mm, 81 parts (8 on the bottom side), 64 nets.

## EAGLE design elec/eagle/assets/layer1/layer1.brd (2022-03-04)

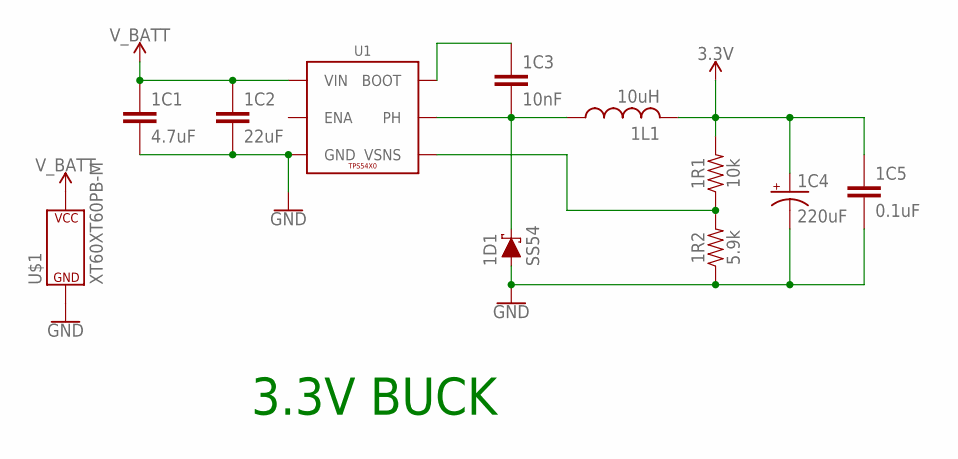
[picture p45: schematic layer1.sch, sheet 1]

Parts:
1C1: 4.7uF; C0603
1C2: 22uF; C1210
1C3: 10nF; C0603
1C4: 220uF; EIA7343
1C5: 0.1uF; C0603
1D1: SS54; SMA-DIODE
1L1: 10uH; SWPA8040
1R1: 10k; R0603
1R2: 5.9k; R0603
U1: TPS54X0; POWERPAD-SOIC-8
U$1: XT60XT60PB-M; XT60PB-M

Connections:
3.3V: 1C4.A (+), 1C5.1, 1L1.P2 (2), 1R1.2; also elsewhere on the board
GND: 1C1.2, 1C2.2, 1C4.C (-), 1C5.2, 1D1.A, 1R2.1, U1.6 (GND), U1.9 (GND), U1.P$1 (GND), U1.P$2 (GND), U1.P$3 (GND), U1.P$4 (GND), U1.P$5 (GND), U1.P$6 (GND), U$1.- (V-); also elsewhere on the board
unnamed: 1C3.1, U1.1 (BOOT)
unnamed: 1C3.2, 1D1.C, 1L1.P1 (1), U1.8 (PH)
unnamed: 1R1.1, 1R2.2, U1.4 (VSNS)
V_BATT: 1C1.1, 1C2.1, U1.7 (VIN), U$1.+ (V+); also elsewhere on the board

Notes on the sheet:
3.3V BUCK


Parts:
2C1, 2C2, 2C3: 0.1uF; C0603
2C4, 2C5, 2C6: 1uF; C0603
2R1, 2R2, 2R3: 1k; R0603
2R4, 2R5, 2R6: 3k; R0603
LC1, LC2, LC3, LC4, LC5, LC6: 1uF; C0603
LD1, LD2, LD3, LD4, LD5, LD6, LD7, LD8, LD9, LD10, LD11, LD12, LD13, LD14, LD15, LD16, LD17, LD18, LD19, LD20, LD21, LD22, LD23, LD24, LD25, LD26, LD27, LD28, LD29, LD30, LD31, LD32, LD33, LD34, LD35, LD36: 3528LED; 3528
LDR: CONN_021X02_NO_SILK; 1X02_NO_SILK
LED: CONN_02POLAR; MOLEX-1X2
LG_R2: 2k; R0603
LIGHT_SWITCH: SWITCH-SPDT-PTH-11.6X4.0MM-LOCK; SWITCH_SPDT_PTH_11.6X4.0MM_LOCK
LR1: 47; R0603
MUX_L1, MUX_L2, MUX_L3: 74HC4067SSOP-24; SSOP24
Q1, Q2, Q3, Q4, Q5, Q6, Q7, Q8, Q9, Q10, Q11, Q12, Q13, Q14, Q15, Q16, Q17, Q18, Q19, Q20, Q21, Q22, Q23, Q24, Q25, Q26, Q27, Q28, Q29, Q30, Q31, Q32, Q33, Q34, Q35, Q36: LIGHT_SENSORALS; ALS-PT19

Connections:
3.3V: 2C1.1, 2C2.1, 2C3.1, LIGHT_SWITCH.2, MUX_L1.24 (VCC), MUX_L2.24 (VCC), MUX_L3.24 (VCC); also elsewhere on the board
AGND: 2C4.2, 2C5.2, 2C6.2, 2R4.1, 2R5.1, 2R6.1; also elsewhere on the board
GND: 2C1.2, 2C2.2, 2C3.2, 2R1.1, 2R2.1, 2R3.1, LC1.2, LC2.2, LC3.2, LC4.2, LC5.2, LC6.2, LED.1, LG_R2.1, LR1.2, MUX_L1.12 (GND), MUX_L2.12 (GND), MUX_L3.12 (GND); also elsewhere on the board
LG_SIG: LDR.2, LG_R2.2; also elsewhere on the board
LS0: MUX_L1.10 (S0), MUX_L2.10 (S0), MUX_L3.10 (S0); also elsewhere on the board
LS1: MUX_L1.11 (S1), MUX_L2.11 (S1), MUX_L3.11 (S1); also elsewhere on the board
LS2: MUX_L1.14 (S2), MUX_L2.14 (S2), MUX_L3.14 (S2); also elsewhere on the board
LS3: MUX_L1.13 (S3), MUX_L2.13 (S3), MUX_L3.13 (S3); also elsewhere on the board
LSIG1: 2C4.1, 2R4.2, MUX_L1.1 (COM); also elsewhere on the board
LSIG2: 2C5.1, 2R5.2, MUX_L2.1 (COM); also elsewhere on the board
LSIG3: 2C6.1, 2R6.2, MUX_L3.1 (COM); also elsewhere on the board
LSWITCH: LC1.1, LC2.1, LC3.1, LC4.1, LC5.1, LC6.1, LD1.A, LD2.A, LD3.A, LD4.A, LD5.A, LD6.A, LD7.A, LD8.A, LD9.A, LD10.A, LD11.A, LD12.A, LD13.A, LD14.A, LD15.A, LD16.A, LD17.A, LD18.A, LD19.A, LD20.A, LD21.A, LD22.A, LD23.A, LD24.A, LD25.A, LD26.A, LD27.A, LD28.A, LD29.A, LD30.A, LD31.A, LD32.A, LD33.A, LD34.A, LD35.A, LD36.A, LED.2, LIGHT_SWITCH.1 (O)
unnamed: 2R1.2, MUX_L1.15 (EN)
unnamed: MUX_L1.16 (CHAN15), Q1.E (E1)
unnamed: MUX_L1.17 (CHAN14), Q2.E (E1)
unnamed: MUX_L1.18 (CHAN13), Q3.E (E1)
unnamed: MUX_L1.19 (CHAN12), Q4.E (E1)
unnamed: MUX_L1.20 (CHAN11), Q5.E (E1)
unnamed: MUX_L1.21 (CHAN10), Q6.E (E1)
unnamed: MUX_L1.22 (CHAN9), Q7.E (E1)
unnamed: MUX_L1.23 (CHAN8), Q8.E (E1)
unnamed: MUX_L1.2 (CHAN7), Q9.E (E1)
unnamed: MUX_L1.3 (CHAN6), Q10.E (E1)
unnamed: MUX_L1.4 (CHAN5), Q11.E (E1)
unnamed: MUX_L1.5 (CHAN4), Q12.E (E1)
unnamed: MUX_L1.6 (CHAN3), Q13.E (E1)
unnamed: MUX_L1.7 (CHAN2), Q14.E (E1)
unnamed: MUX_L1.8 (CHAN1), Q15.E (E1)
unnamed: MUX_L1.9 (CHAN0), Q16.E (E1)
unnamed: LD1.C, LD2.C, LD3.C, LD4.C, LD5.C, LD6.C, LD7.C, LD8.C, LD9.C, LD10.C, LD11.C, LD12.C, LD13.C, LD14.C, LD15.C, LD16.C, LD17.C, LD18.C, LD19.C, LD20.C, LD21.C, LD22.C, LD23.C, LD24.C, LD25.C, LD26.C, LD27.C, LD28.C, LD29.C, LD30.C, LD31.C, LD32.C, LD33.C, LD34.C, LD35.C, LD36.C, LR1.1
unnamed: 2R2.2, MUX_L2.15 (EN)
unnamed: MUX_L2.16 (CHAN15), Q17.E (E1)
unnamed: MUX_L2.17 (CHAN14), Q18.E (E1)
unnamed: MUX_L2.18 (CHAN13), Q19.E (E1)
unnamed: MUX_L2.19 (CHAN12), Q20.E (E1)
unnamed: MUX_L2.20 (CHAN11), Q21.E (E1)
unnamed: MUX_L2.21 (CHAN10), Q22.E (E1)
unnamed: MUX_L2.22 (CHAN9), Q23.E (E1)
unnamed: MUX_L2.23 (CHAN8), Q24.E (E1)
unnamed: MUX_L2.2 (CHAN7), Q25.E (E1)
unnamed: MUX_L2.3 (CHAN6), Q26.E (E1)
unnamed: MUX_L2.4 (CHAN5), Q27.E (E1)
unnamed: MUX_L2.5 (CHAN4), Q28.E (E1)
unnamed: MUX_L2.6 (CHAN3), Q29.E (E1)
unnamed: MUX_L2.7 (CHAN2), Q30.E (E1)
unnamed: MUX_L2.8 (CHAN1), Q31.E (E1)
unnamed: MUX_L2.9 (CHAN0), Q32.E (E1)
unnamed: 2R3.2, MUX_L3.15 (EN)
unnamed: MUX_L3.16 (CHAN15), Q33.E (E1)
unnamed: MUX_L3.17 (CHAN14), Q34.E (E1)
unnamed: MUX_L3.18 (CHAN13), Q35.E (E1)
unnamed: MUX_L3.19 (CHAN12), Q36.E (E1)
VCCA: LDR.1, Q1.C (C1), Q2.C (C1), Q3.C (C1), Q4.C (C1), Q5.C (C1), Q6.C (C1), Q7.C (C1), Q8.C (C1), Q9.C (C1), Q10.C (C1), Q11.C (C1), Q12.C (C1), Q13.C (C1), Q14.C (C1), Q15.C (C1), Q16.C (C1), Q17.C (C1), Q18.C (C1), Q19.C (C1), Q20.C (C1), Q21.C (C1), Q22.C (C1), Q23.C (C1), Q24.C (C1), Q25.C (C1), Q26.C (C1), Q27.C (C1), Q28.C (C1), Q29.C (C1), Q30.C (C1), Q31.C (C1), Q32.C (C1), Q33.C (C1), Q34.C (C1), Q35.C (C1), Q36.C (C1); also elsewhere on the board

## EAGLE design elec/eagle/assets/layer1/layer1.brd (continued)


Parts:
3C1, 3C2: 0.1uF; C0603
M1C1, M2C1, M3C1, M4C1: 33nF; C0603
M1C2, M2C2, M3C2, M4C2: 680uF; 3.5MM_CAP
M1C3, M2C3, M3C3, M4C3: 1.0uF; C0603
M1D1, M2D1, M3D1, M4D1: RED; LED-0603
M1D2, M2D2, M3D2, M4D2: BLUE; LED-0603
M1J1, M2J1, M3J1, M4J1: XT30PB-F
M1Q1, M2Q1, M3Q1, M4Q1: AOD482; DPAK
M1R1, M1R2, M1R5, M1R6, M1R7, M1R10, M2R1, M2R2, M2R5, M2R6, M2R7, M2R10, M3R1, M3R2, M3R5, M3R6, M3R7, M3R10, M4R1, M4R2, M4R5, M4R6, M4R7, M4R10: 1k; R0603
M1R3, M1R4, M2R3, M2R4, M3R3, M3R4, M4R3, M4R4: 3.3k; R0603
M1R8, M1R9, M1R11, M2R8, M2R9, M2R11, M3R8, M3R9, M3R11, M4R8, M4R9, M4R11: 10k; R0603
M1R12, M2R12, M3R12, M4R12: 4.7k; R0603
MOTOR_SWITCH: SWITCH-SPDT-PTH-11.6X4.0MM-LOCK; SWITCH_SPDT_PTH_11.6X4.0MM_LOCK
MU1, MU2: SN74LVC2G04DBVR; SOT23-6
M_BL: VNH5019; POWERSO-30
M_BR: VNH5019; POWERSO-30
M_FL: VNH5019; POWERSO-30
M_FR: VNH5019; POWERSO-30
V_BATT_M1A, V_BATT_M1B, V_BATT_M2A, V_BATT_M2B, V_BATT_M3A, V_BATT_M3B, V_BATT_M4A, V_BATT_M4B: 18AWG

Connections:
3.3V: 3C1.1, 3C2.1, M1R3.2, M1R4.2, M2R3.2, M2R4.2, M3R3.2, M3R4.2, M4R3.2, M4R4.2, MU1.5 (VCC), MU2.5 (VCC); also elsewhere on the board
BL_CS: M3C1.1, M3R8.1; also elsewhere on the board
BL_DIR: M3R5.1, MU2.1 (1A); also elsewhere on the board
BL_OUTA: M3D1.C, M3D2.A, M3J1.+ (V+), M_BL.P1 (OUT_A), M_BL.P25 (OUT_A), M_BL.P30 (OUT_A), M_BL.P$1 (OUT_A), M_BL.P$2 (OUT_A), M_BL.P$3 (OUT_A), M_BL.P$4 (OUT_A), M_BL.P$5 (OUT_A), M_BL.P$6 (OUT_A), M_BL.P$7 (OUT_A), M_BL.P$8 (OUT_A), M_BL.P$9 (OUT_A), M_BL.SLUG2 (OUT_A)
BL_OUTB: M3J1.- (V-), M3R12.2, M_BL.P15 (OUT_B), M_BL.P16 (OUT_B), M_BL.P21 (OUT_B), M_BL.P$10 (OUT_B), M_BL.P$11 (OUT_B), M_BL.P$12 (OUT_B), M_BL.P$13 (OUT_B), M_BL.P$14 (OUT_B), M_BL.P$15 (OUT_B), M_BL.P$16 (OUT_B), M_BL.P$17 (OUT_B), M_BL.P$18 (OUT_B), M_BL.SLUG3 (OUT_B)
BL_PWM: M3R7.1, M3R11.2; also elsewhere on the board
BR_CS: M4C1.1, M4R8.1; also elsewhere on the board
BR_DIR: M4R5.1, MU2.3 (2A); also elsewhere on the board
BR_OUTA: M4D1.C, M4D2.A, M4J1.+ (V+), M_BR.P1 (OUT_A), M_BR.P25 (OUT_A), M_BR.P30 (OUT_A), M_BR.P$1 (OUT_A), M_BR.P$2 (OUT_A), M_BR.P$3 (OUT_A), M_BR.P$4 (OUT_A), M_BR.P$5 (OUT_A), M_BR.P$6 (OUT_A), M_BR.P$7 (OUT_A), M_BR.P$8 (OUT_A), M_BR.P$9 (OUT_A), M_BR.SLUG2 (OUT_A)
BR_OUTB: M4J1.- (V-), M4R12.2, M_BR.P15 (OUT_B), M_BR.P16 (OUT_B), M_BR.P21 (OUT_B), M_BR.P$10 (OUT_B), M_BR.P$11 (OUT_B), M_BR.P$12 (OUT_B), M_BR.P$13 (OUT_B), M_BR.P$14 (OUT_B), M_BR.P$15 (OUT_B), M_BR.P$16 (OUT_B), M_BR.P$17 (OUT_B), M_BR.P$18 (OUT_B), M_BR.SLUG3 (OUT_B)
BR_PWM: M4R7.1, M4R11.2; also elsewhere on the board
FL_CS: M1C1.1, M1R8.1; also elsewhere on the board
FL_DIR: M1R5.1, MU1.1 (1A); also elsewhere on the board
FL_OUTA: M1D1.C, M1D2.A, M1J1.+ (V+), M_FL.P1 (OUT_A), M_FL.P25 (OUT_A), M_FL.P30 (OUT_A), M_FL.P$1 (OUT_A), M_FL.P$2 (OUT_A), M_FL.P$3 (OUT_A), M_FL.P$4 (OUT_A), M_FL.P$5 (OUT_A), M_FL.P$6 (OUT_A), M_FL.P$7 (OUT_A), M_FL.P$8 (OUT_A), M_FL.P$9 (OUT_A), M_FL.SLUG2 (OUT_A)
FL_OUTB: M1J1.- (V-), M1R12.2, M_FL.P15 (OUT_B), M_FL.P16 (OUT_B), M_FL.P21 (OUT_B), M_FL.P$10 (OUT_B), M_FL.P$11 (OUT_B), M_FL.P$12 (OUT_B), M_FL.P$13 (OUT_B), M_FL.P$14 (OUT_B), M_FL.P$15 (OUT_B), M_FL.P$16 (OUT_B), M_FL.P$17 (OUT_B), M_FL.P$18 (OUT_B), M_FL.SLUG3 (OUT_B)
FL_PWM: M1R7.1, M1R11.2; also elsewhere on the board
FR_CS: M2C1.1, M2R8.1; also elsewhere on the board
FR_DIR: M2R5.1, MU1.3 (2A); also elsewhere on the board
FR_OUTA: M2D1.C, M2D2.A, M2J1.+ (V+), M_FR.P1 (OUT_A), M_FR.P25 (OUT_A), M_FR.P30 (OUT_A), M_FR.P$1 (OUT_A), M_FR.P$2 (OUT_A), M_FR.P$3 (OUT_A), M_FR.P$4 (OUT_A), M_FR.P$5 (OUT_A), M_FR.P$6 (OUT_A), M_FR.P$7 (OUT_A), M_FR.P$8 (OUT_A), M_FR.P$9 (OUT_A), M_FR.SLUG2 (OUT_A)
FR_OUTB: M2J1.- (V-), M2R12.2, M_FR.P15 (OUT_B), M_FR.P16 (OUT_B), M_FR.P21 (OUT_B), M_FR.P$10 (OUT_B), M_FR.P$11 (OUT_B), M_FR.P$12 (OUT_B), M_FR.P$13 (OUT_B), M_FR.P$14 (OUT_B), M_FR.P$15 (OUT_B), M_FR.P$16 (OUT_B), M_FR.P$17 (OUT_B), M_FR.P$18 (OUT_B), M_FR.SLUG3 (OUT_B)
FR_PWM: M2R7.1, M2R11.2; also elsewhere on the board
GND: 3C1.2, 3C2.2, M1C1.2, M1C2.2 (-), M1C3.2, M1R9.1, M1R10.1, M1R11.1, M2C1.2, M2C2.2 (-), M2C3.2, M2R9.1, M2R10.1, M2R11.1, M3C1.2, M3C2.2 (-), M3C3.2, M3R9.1, M3R10.1, M3R11.1, M4C1.2, M4C2.2 (-), M4C3.2, M4R9.1, M4R10.1, M4R11.1, MOTOR_SWITCH.1 (O), MU1.2 (GND), MU2.2 (GND), M_BL.P18 (GND), M_BL.P19 (GND), M_BL.P20 (GND), M_BL.P26 (GND), M_BL.P27 (GND), M_BL.P28 (GND), M_BR.P18 (GND), M_BR.P19 (GND), M_BR.P20 (GND), M_BR.P26 (GND), M_BR.P27 (GND), M_BR.P28 (GND), M_FL.P18 (GND), M_FL.P19 (GND), M_FL.P20 (GND), M_FL.P26 (GND), M_FL.P27 (GND), M_FL.P28 (GND), M_FR.P18 (GND), M_FR.P19 (GND), M_FR.P20 (GND), M_FR.P26 (GND), M_FR.P27 (GND), M_FR.P28 (GND); also elsewhere on the board
M_SWITCH: M1R1.1, M1R2.1, M2R1.1, M2R2.1, M3R1.1, M3R2.1, M4R1.1, M4R2.1, MOTOR_SWITCH.2
unnamed: M1R1.2, M1R4.1, M_FL.P5 (EN_A)
unnamed: M1R2.2, M1R3.1, M_FL.P9 (EN_B)
unnamed: M1R5.2, M_FL.P4 (IN_A)
unnamed: M1R6.2, M_FL.P10 (IN_B)
unnamed: M1R7.2, M_FL.P7 (PWM_IN)
unnamed: M1R8.2, M1R10.2, M_FL.P8 (CS)
unnamed: M1R9.2, M_FL.P6 (CS_DIS)
unnamed: M1C2.1 (+), M1C3.1, M1Q1.4 (D), M_FL.P3 (VCC), M_FL.P13 (VCC), M_FL.P23 (VCC), M_FL.P$19 (VCC), M_FL.P$20 (VCC), M_FL.P$21 (VCC), M_FL.P$22 (VCC), M_FL.P$23 (VCC), M_FL.P$24 (VCC), M_FL.P$25 (VCC), M_FL.P$26 (VCC), M_FL.P$27 (VCC), M_FL.P$28 (VCC), M_FL.SLUG1 (VCC)
unnamed: M1Q1.1 (G), M_FL.P11 (CP)
unnamed: M2R2.2, M2R3.1, M_FR.P9 (EN_B)
unnamed: M1D1.A, M1D2.C, M1R12.1
unnamed: M2R1.2, M2R4.1, M_FR.P5 (EN_A)
unnamed: M2R6.2, M_FR.P10 (IN_B)
unnamed: M2R5.2, M_FR.P4 (IN_A)
unnamed: M2R7.2, M_FR.P7 (PWM_IN)
unnamed: M2R8.2, M2R10.2, M_FR.P8 (CS)
unnamed: M2R9.2, M_FR.P6 (CS_DIS)
unnamed: M2C2.1 (+), M2C3.1, M2Q1.4 (D), M_FR.P3 (VCC), M_FR.P13 (VCC), M_FR.P23 (VCC), M_FR.P$19 (VCC), M_FR.P$20 (VCC), M_FR.P$21 (VCC), M_FR.P$22 (VCC), M_FR.P$23 (VCC), M_FR.P$24 (VCC), M_FR.P$25 (VCC), M_FR.P$26 (VCC), M_FR.P$27 (VCC), M_FR.P$28 (VCC), M_FR.SLUG1 (VCC)
unnamed: M2Q1.1 (G), M_FR.P11 (CP)
unnamed: M3R2.2, M3R3.1, M_BL.P9 (EN_B)
unnamed: M2D1.A, M2D2.C, M2R12.1
unnamed: M3R1.2, M3R4.1, M_BL.P5 (EN_A)
unnamed: M3R6.2, M_BL.P10 (IN_B)
unnamed: M3R5.2, M_BL.P4 (IN_A)
unnamed: M3R7.2, M_BL.P7 (PWM_IN)
unnamed: M3R8.2, M3R10.2, M_BL.P8 (CS)
unnamed: M3R9.2, M_BL.P6 (CS_DIS)
unnamed: M3C2.1 (+), M3C3.1, M3Q1.4 (D), M_BL.P3 (VCC), M_BL.P13 (VCC), M_BL.P23 (VCC), M_BL.P$19 (VCC), M_BL.P$20 (VCC), M_BL.P$21 (VCC), M_BL.P$22 (VCC), M_BL.P$23 (VCC), M_BL.P$24 (VCC), M_BL.P$25 (VCC), M_BL.P$26 (VCC), M_BL.P$27 (VCC), M_BL.P$28 (VCC), M_BL.SLUG1 (VCC)
unnamed: M3Q1.1 (G), M_BL.P11 (CP)
unnamed: M4R2.2, M4R3.1, M_BR.P9 (EN_B)
unnamed: M4R1.2, M4R4.1, M_BR.P5 (EN_A)
unnamed: M4R6.2, M_BR.P10 (IN_B)
unnamed: M4R5.2, M_BR.P4 (IN_A)
unnamed: M4R7.2, M_BR.P7 (PWM_IN)
unnamed: M3D1.A, M3D2.C, M3R12.1
unnamed: M4R8.2, M4R10.2, M_BR.P8 (CS)
unnamed: M4R9.2, M_BR.P6 (CS_DIS)
unnamed: M4C2.1 (+), M4C3.1, M4Q1.4 (D), M_BR.P3 (VCC), M_BR.P13 (VCC), M_BR.P23 (VCC), M_BR.P$19 (VCC), M_BR.P$20 (VCC), M_BR.P$21 (VCC), M_BR.P$22 (VCC), M_BR.P$23 (VCC), M_BR.P$24 (VCC), M_BR.P$25 (VCC), M_BR.P$26 (VCC), M_BR.P$27 (VCC), M_BR.P$28 (VCC), M_BR.SLUG1 (VCC)
unnamed: M4Q1.1 (G), M_BR.P11 (CP)
unnamed: M4D1.A, M4D2.C, M4R12.1
NOT_BL_DIR: M3R6.1, MU2.6 (1Y)
NOT_BR_DIR: M4R6.1, MU2.4 (2Y)
NOT_FL_DIR: M1R6.1, MU1.6 (1Y)
NOT_FR_DIR: M2R6.1, MU1.4 (2Y)
V_BATT: M1Q1.3 (S), M2Q1.3 (S), M3Q1.3 (S), M4Q1.3 (S), M_BL.P12 (VBAT), M_BR.P12 (VBAT), M_FL.P12 (VBAT), M_FR.P12 (VBAT), V_BATT_M1A.P$1, V_BATT_M1B.P$1, V_BATT_M2A.P$1, V_BATT_M2B.P$1, V_BATT_M3A.P$1, V_BATT_M3B.P$1, V_BATT_M4A.P$1, V_BATT_M4B.P$1; also elsewhere on the board


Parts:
BOOT: MOMENTARY_SWITCH_4X3
C1, C2, C3, C5, C8: 1uF; C0603
C4: 10nF; C0603
C6, C7: 22pF; C0603
D1: STM_LED; LED-0603
FB1, FB2: 30Ω/1.8A; 0603
J2: CONN_03LOCK_NO_SILK; 1X03_LOCK_NO_SILK
R1, R4, R10: 10k; R0603
R2, R3: 1k; R0603
R5: 470; R0603
R6: 2M; R0603
R7: 500k; R0603
RST: MOMENTARY_SWITCH_4X3
U$2: STM32F103CBT6; LQFP48
U$15: CONN_07X2; 2X7
X2: SM06B-SRSS-TB
Y1: 8MHz; CRYSTAL-SMD-5X3.2-2PAD

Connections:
3.3V: C1.1, C2.1, C3.1, C8.1, FB1.1, J2.1, R1.2, R3.2, U$2.1 (VBAT), U$2.24 (VDD_1), U$2.36 (VDD_2), U$2.48 (VDD_3), U$15.13, X2.4; also elsewhere on the board
AGND: C4.1, C5.1, FB2.2, U$2.8 (VSS_A); also elsewhere on the board
BATT_LVL: R6.1, R7.2, U$15.12
BL_CS: U$2.16 (PA6/SPI1_MISO/ADC12_IN6/TIM3_CH1); also elsewhere on the board
BL_DIR: U$15.5; also elsewhere on the board
BL_PWM: U$15.6; also elsewhere on the board
BOOT0: BOOT.P$2 (2), R4.2, U$2.44 (BOOT0), U$2.45 (PB8/TIM4_CH3)
BR_CS: U$2.17 (PA7/SPI1_MOSI/ADC12_IN7/TIM3_CH2); also elsewhere on the board
BR_DIR: U$15.7; also elsewhere on the board
BR_PWM: U$15.8; also elsewhere on the board
FL_CS: U$2.14 (PA4/SPI1_NSS/USART2_CK/ADC12_IN4); also elsewhere on the board
FL_DIR: U$15.1; also elsewhere on the board
FL_PWM: U$15.2; also elsewhere on the board
FR_CS: U$2.15 (PA5/SPI1_SCK/ADC12_IN5); also elsewhere on the board
FR_DIR: U$15.3; also elsewhere on the board
FR_PWM: U$15.4; also elsewhere on the board
GND: C1.2, C2.2, C3.2, C6.1, C7.1, C8.2, D1.C, FB2.1, R2.1, R4.1, R7.1, R10.1, U$2.23 (VSS_1), U$2.35 (VSS_2), U$2.47 (VSS_3), U$15.14, X2.1; also elsewhere on the board
LG_SIG: U$2.13 (PA3/USART2_RX/ADC12_IN3/TIM2_CH4); also elsewhere on the board
LIGHT_INT: U$2.29 (PA8/USART1_CK/TIM1_CH1/MCO), U$15.10
LIMIT_SWITCH: J2.2, R10.2, U$2.40 (PB4/NJTRST)
LS0: U$2.25 (PB12/SPI2_NSS/I2C2_SMBA/USART3_CK/TIM1_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); also elsewhere on the board
LS1: U$2.26 (PB13/SPI2_SCK/USART3_CTS/TIM1_CH1N); also elsewhere on the board
LS2: U$2.27 (PB14/SPI2_MISO/USART3_RTS/TIM1_CH2N); also elsewhere on the board
LS3: U$2.28 (PB15/SPI2_MOSI/TIM1_CH3N); also elsewhere on the board
LSIG1: U$2.10 (PA0_WKUP/USART2_CTS/ADC12_IN0/TIM2_CH1_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); also elsewhere on the board
LSIG2: U$2.11 (PA1/USART2_RTS/ADC12_IN1/TIM2_CH2); also elsewhere on the board
LSIG3: U$2.12 (PA2/USART2_TX/ADC12_IN2/TIM2_CH3); also elsewhere on the board
unnamed: R2.2, RST.P$1 (1)
unnamed: BOOT.P$1 (1), R3.1
unnamed: R5.2, U$2.18 (PB0/ADC12_IN8/TIM3_CH3)
unnamed: D1.A, R5.1
OSC_IN: C6.2, U$2.5 (PD0-OSC_IN), Y1.P$2 (2)
OSC_OUT: C7.2, U$2.6 (PD1-OSC_OUT), Y1.P$1 (1)
RESET: R1.1, RST.P$2 (2), U$2.7 (NRST)
RX1: U$2.31 (PA10/USART1_RX/TIM1_CH3), X2.6
RX3: U$2.22 (PB11/I2C2_SDA/USART3_RX), U$15.11
SWCLK: U$2.37 (PA14/JTCK/SWCLK), X2.2
SWDIO: U$2.34 (PA13/JTMS/SWDIO), X2.3
TX1: U$2.30 (PA9/USART1_TX/TIM1_CH2), X2.5
TX3: U$2.21 (PB10/I2C2_SCL/USART3_TX), U$15.9
VCCA: C4.2, C5.2, FB1.2, U$2.9 (VDD_A); also elsewhere on the board
V_BATT: R6.2; also elsewhere on the board

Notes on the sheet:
LIMIT_SWITCH


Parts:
1C6: 4.7uF; C0603
1C7: 220uF; EIA7343
1C8: 10nF; C0603
1C9: 0.1uF; C0603
1C10: 22uF; C1210
1D2: SS54; SMA-DIODE
1L2: 10uH; SWPA8040
1R3: 10k; R0603
1R4: 3.24k; R0603
ESC_IN: CONN_03LOCK; 1X03_LOCK
ESC_OUT: XT30PB-F
GND: CONN_01; 1X01
J1: CONN_02LOCK; 1X02_LOCK
Q37: AO3402; SOT23-3
R8, R9: 4.7k; R0603
U2: TPS54X0; POWERPAD-SOIC-8

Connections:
3.3V1: Q37.1 (G), R9.1
5V: 1C7.A (+), 1C9.1, 1L2.P2 (2), 1R3.2, J1.2, R8.1
ESC_HV: ESC_IN.3, Q37.3 (D), R8.2
ESC_LV: J1.1, Q37.2 (S), R9.2
GND: 1C6.2, 1C7.C (-), 1C9.2, 1C10.2, 1D2.A, 1R4.1, ESC_IN.1, ESC_OUT.- (V-), GND.1, U2.6 (GND), U2.9 (GND), U2.P$1 (GND), U2.P$2 (GND), U2.P$3 (GND), U2.P$4 (GND), U2.P$5 (GND), U2.P$6 (GND); also elsewhere on the board
unnamed: 1C8.2, 1D2.C, 1L2.P1 (1), U2.8 (PH)
unnamed: 1R3.1, 1R4.2, U2.4 (VSNS)
unnamed: 1C8.1, U2.1 (BOOT)
V_BATT: 1C6.1, 1C10.1, ESC_OUT.+ (V+), U2.7 (VIN); also elsewhere on the board

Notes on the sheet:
5V BUCK



Board: 2 copper layers, 196.0 x 185.3 mm, 245 parts (92 on the bottom side), 146 nets.

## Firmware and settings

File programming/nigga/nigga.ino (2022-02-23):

#include <i2c_t3.h>
#include <Adafruit_Sensor.h>
#include <Adafruit_BNO055_t3.h>
#include <utility/imumaths.h>

/* This driver uses the Adafruit unified sensor library (Adafruit_Sensor),
   which provides a common 'type' for sensor data and some helper functions.

   To use this driver you will also need to download the Adafruit_Sensor
   library and include it in your libraries folder.

   You should also assign a unique ID to this sensor for use with
   the Adafruit Sensor API so that you can identify this particular
   sensor in any data logs, etc.  To assign a unique ID, simply
   provide an appropriate value in the constructor below (12345
   is used by default in this example).

   Connections
   ===========
   Connect SCL to analog 5
   Connect SDA to analog 4
   Connect VDD to 3.3-5V DC
   Connect GROUND to common ground

   History
   =======
   2015/MAR/03  - First release (KTOWN)
*/

/* Set the delay between fresh samples */
uint16_t BNO055_SAMPLERATE_DELAY_MS = 100;

// Check I2C device address and correct line below (by default address is 0x29 or 0x28)
//                                   id, address
Adafruit_BNO055 bno = Adafruit_BNO055(WIRE1_BUS, -1, BNO055_ADDRESS_A, I2C_MASTER, I2C_PINS_18_19, I2C_PULLUP_EXT, I2C_RATE_100, I2C_OP_MODE_ISR);

void setup(void)
{
  Serial.begin(115200);
  Serial.println("Orientation Sensor Test"); Serial.println("");

  /* Initialise the sensor */
  if (!bno.begin())
  {
    /* There was a problem detecting the BNO055 ... check your connections */
    Serial.print("Ooops, no BNO055 detected ... Check your wiring or I2C ADDR!");
    while (1);
  }

  delay(1000);
}

void loop(void)
{
  //could add VECTOR_ACCELEROMETER, VECTOR_MAGNETOMETER,VECTOR_GRAVITY...
  sensors_event_t orientationData , angVelocityData , linearAccelData, magnetometerData, accelerometerData, gravityData;
  bno.getEvent(&orientationData, Adafruit_BNO055::VECTOR_EULER);
  bno.getEvent(&angVelocityData, Adafruit_BNO055::VECTOR_GYROSCOPE);
  bno.getEvent(&linearAccelData, Adafruit_BNO055::VECTOR_LINEARACCEL);
  bno.getEvent(&magnetometerData, Adafruit_BNO055::VECTOR_MAGNETOMETER);
  bno.getEvent(&accelerometerData, Adafruit_BNO055::VECTOR_ACCELEROMETER);
  bno.getEvent(&gravityData, Adafruit_BNO055::VECTOR_GRAVITY);

  printEvent(&orientationData);
  printEvent(&angVelocityData);
  printEvent(&linearAccelData);
  printEvent(&magnetometerData);
  printEvent(&accelerometerData);
  printEvent(&gravityData);

  int8_t boardTemp = bno.getTemp();
  Serial.println();
  Serial.print(F("temperature: "));
  Serial.println(boardTemp);

  uint8_t system, gyro, accel, mag = 0;
  bno.getCalibration(&system, &gyro, &accel, &mag);
  Serial.println();
  Serial.print("Calibration: Sys=");
  Serial.print(system);
  Serial.print(" Gyro=");
  Serial.print(gyro);
  Serial.print(" Accel=");
  Serial.print(accel);
  Serial.print(" Mag=");
  Serial.println(mag);

  Serial.println("--");
  delay(BNO055_SAMPLERATE_DELAY_MS);
}

void printEvent(sensors_event_t* event) {
  double x = -1000000, y = -1000000 , z = -1000000; //dumb values, easy to spot problem
  if (event->type == SENSOR_TYPE_ACCELEROMETER) {
    Serial.print("Accl:");
    x = event->acceleration.x;
    y = event->acceleration.y;
    z = event->acceleration.z;
  }
  else if (event->type == SENSOR_TYPE_ORIENTATION) {
    Serial.print("Orient:");
    x = event->orientation.x;
    y = event->orientation.y;
    z = event->orientation.z;
  }
  else if (event->type == SENSOR_TYPE_MAGNETIC_FIELD) {
    Serial.print("Mag:");
    x = event->magnetic.x;
    y = event->magnetic.y;
    z = event->magnetic.z;
  }
  else if (event->type == SENSOR_TYPE_GYROSCOPE) {
    Serial.print("Gyro:");
    x = event->gyro.x;
    y = event->gyro.y;
    z = event->gyro.z;
  }
  else if (event->type == SENSOR_TYPE_ROTATION_VECTOR) {
    Serial.print("Rot:");
    x = event->gyro.x;
    y = event->gyro.y;
    z = event->gyro.z;
  }
  else if (event->type == SENSOR_TYPE_LINEAR_ACCELERATION) {
    Serial.print("Linear:");
    x = event->acceleration.x;
    y = event->acceleration.y;
    z = event->acceleration.z;
  }
  else if (event->type == SENSOR_TYPE_GRAVITY) {
    Serial.print("Gravity:");
    x = event->acceleration.x;
    y = event->acceleration.y;
    z = event->acceleration.z;
  }
  else {
    Serial.print("Unk:");
  }

  Serial.print("\tx= ");
  Serial.print(x);
  Serial.print(" |\ty= ");
  Serial.print(y);
  Serial.print(" |\tz= ");
  Serial.println(z);
}

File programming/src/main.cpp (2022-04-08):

#include <Arduino.h>
#include <i2c_t3.h>
#include <Adafruit_Sensor.h>
#include <Adafruit_BNO055_t3.h>
#include <utility/imumaths.h>
#include <math.h>

void setup(){
    // PWM 22
    // DIR 21
    pinMode(21,OUTPUT);
    pinMode(22,OUTPUT);
}

void loop(){
    analogWrite(21,255);
    digitalWrite(22,HIGH);
    delay(1000);
}

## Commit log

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2021-11-23 added stl folder in dwg
    [motorspacers.stl]
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2021-11-23 Added the face of the kicker
    [kicker.dwg]
2021-11-23 changed motor spacers design
    [motorspacers.dwg]
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2021-11-23 added kicker .stl and .gcode
    [kicker.dwg, kicker.stl]
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2021-11-24 sort of done with final
    [layer2.dwg]
2021-11-24 change kicker height in final + added prototype
    [kicker-head-1.dwg, kicker-head-2.dwg]
2021-11-25 added gcode and stl
    [dribblermount.stl]
2021-11-25 updated dribbler mount & plate, added dribbler spaces
    [dribblermountv2.stl, dribblerplate.stl, dribblerspacer.stl]
2021-11-26 updated motor mount and added missing holes for motor to layer 2
    [dribblermountv3.stl]
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2021-11-28 added dxf files for layer 3 and 4
    [layer3.dxf, layer4.dxf]
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2021-11-29 cancer pain in the ass
    [Layer 3.brd]
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2021-12-01 added layer 4 file
    [layer4.brd]
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2021-12-01 more shit need to do
    [layer4.brd]
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2021-12-01 done with layer 4
    [Layer 3.brd, layer4.brd, layer4.sch]
2021-12-01 changes to layout in layer 3
    [Layer 3.brd]
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2021-12-06 did sanity check on bot
    [Handle.dxf, layer1.dxf]
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2021-12-06 updated layer 3 dxf
    [Layer 3.csv, layer3.dxf, layer4.brd]
2021-12-06 done with layer 3 schem
    [Layer 3.brd, layer3.dxf]
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2022-01-11 modelled new kicker and updated layer1.dxf
    [layer1.dxf]
2022-01-12 modelled new kicker and created kicker parts stl files
    [kickermountleft.stl, kickermountright.stl, kickerv2.stl]
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2022-01-14 added old folder in .dxf
    [layer1.dxf, layer2.dxf, layer3.dxf]
2022-01-15 added .iges and removed switch hole from layer 2
    [2mm Stands.iges, Kicker Body.iges, Kicker Copper Back 1.iges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]
2022-01-15 Updated Layer 3 with new DXF
    [Kicker Mount Left.iges, Kicker Mount Right.iges, Layer 2 to 3 Stands.iges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]
2022-01-15 Added word to handle
    [Handle.iges, Layer 3 to 4 Stands.iges, Layer 3.brd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]
2022-01-17 🚀🚀🚀 Edited Layer 3 and 4 Changed the positioning of the BT Module Change the positioning of the connectors
    [Layer 3.brd, layer4.brd]
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2022-01-18 🥰 Layer 3 Edits Changed oreintation of XH Connectors Shrunk the radius of IR Sensor
    [Layer 3.brd]
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2022-01-19 💀 Almost died again thank god hv backup
    [Layer 3.brd, layer4.brd]
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2022-01-20 tried gear in autocad but failed
    [gearandgearrack.dwg]
2022-01-20 updated kicker to v4, corrected slanted faces on kicker
    [kickerv4.stl]
2022-01-20 added old directory in eagle/assets
    [Layer 1.brd, Layer 1.sch]
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2022-01-20 cut holes in layer 4 and added dxf layer 4 v2
    [layer4.dxf, layer4v2.dxf]
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2022-01-20 🦅 Included Layer 4 new
    [layer4.brd, layer4v2.dxf]
2022-01-20 🦅 Edited Layer 3 Testing Git LFS
    [Handle.iges, Layer 3 to 4 Stands.iges, Layer 3.brd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]
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2022-01-21 added mg90s servo dwg model
    [2mm Stands.iges, Bunny-LowPoly.stl, HIVE_Deep_Drawer.stl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]
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2022-01-21 halfway done with servo mount
    [final-main.dwg]
2022-01-21 Made the servo mount Havent added holes
    [final-main.dwg]
2022-01-21 🦅 Layer 3 AGAIN
    [Layer 3 v22.step, Layer 3.brd, final-main.dwg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]
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2022-01-24 cut holes in layer 2 and 3 for servo mount and update dxf (not plotted and no ai files yet)
    [layer2v2.dxf, layer2v3.dxf, layer3v2.dxf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]
2022-01-26 cut mirrored hole in layer 2
    [layer2v3.dxf, layer2v4.dxf]
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2022-01-27 121 airwires left mostly stm32
    [Layer 1.brd]
2022-01-27 routed some to STEM32
    [Layer 1.brd]
2022-01-27 Added A shit ton of polygons arnd the motor
    [Layer 1.brd]
2022-01-27 Added a shit ton of polygons
    [Layer 1.brd]
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2022-01-28 Done with layer 1
    [Layer 1.brd]
2022-01-28 fuck eagle dying again
    [layer3test.dxf]
2022-02-05 edited layer 1 holes to vias
    [Layer 1.brd, Layer 3.brd]
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2022-02-05 redid layer 1 paining
    [Layer 1.brd]
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2022-02-06 edited layer 3 bt module
    [Layer 3.brd]
2022-02-06 edited layer 3 vias
    [Layer 3.brd]
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2022-02-08 layer 2 dxf not completed
    [layer2v5.dxf]
2022-02-09 updated layer 5 dxf (v5)
    [layer2v5.dxf]
2022-02-09 exported new stl files
    [kickermountleftv3.stl, kickermountleftv4.stl, kickermountrightv3.stl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]
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2022-02-09 all parts here but quite messy
    [Taobao.xlsx]
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2022-02-11 drew new layer 2 dxf (v7)
    [layer1.5.dxf, layer2v4.dxf, layer2v6.dxf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]
2022-02-11 updated all layers dxf
    [layer1v3.dxf, layer1v4.dxf, layer2v7.dxf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]
2022-02-11 updated all layers dxf recommit
    [layer1v5.dxf]
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2022-02-11 moved layer 1 again
    [layer1v5.dxf, layer1v6.dxf, layer1v7.dxf]
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2022-02-11 completed layer1, vincent check now
    [Layer 1.brd]
2022-02-11 aligned layers 3 and 4 to geom center in dxf files
    [a2212motor.dwg, dribbler.dwg, layer3v5.dxf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]
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2022-02-18 layers 1, 3, 4 complete, layer 2 need to change holes to green color thingy?
    [Layer 3.brd]
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2022-02-21 fixed issues on layer 1
    [Layer 1.brd]
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2022-02-21 Fixed a wire stub
2022-02-21 Fixed more stuff
    [Layer 1.brd]
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2022-02-23 Removed Motor Ground and Added battery mount holes
    [Layer 1.brd, Layer 1.sch, layer1v11.dxf]
2022-02-23 fucking done pls vincent dont touch it AGAIN
    [Layer 1.brd, layer1v11.dxf]
2022-02-24 Removed Layer 4 and moved all layer 4 to 3
    [Layer 3.brd, Layer 3.sch, layer4.brd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]
2022-02-24 Redoing the positioning of the motor driver power supply and changed the battery mount holes
    [Layer 1.brd, Layer 3.brd, layer1v11.dxf]
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2022-03-02 fuck man i paid 4 bucks for this
    [sen_white spline.dxf, sen_white.dwg, sen_white.dxf]
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2022-04-08 fixed buggy graphics folder gi
    [sen_vert.dwg, sen_white spline.dxf, sen_white.dwg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]
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

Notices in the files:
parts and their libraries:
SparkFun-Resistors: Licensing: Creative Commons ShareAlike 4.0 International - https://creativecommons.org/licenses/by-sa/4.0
